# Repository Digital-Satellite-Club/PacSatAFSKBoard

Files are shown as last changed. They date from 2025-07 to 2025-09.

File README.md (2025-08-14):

# PacSatAFSKBoard
Hardware design for the PacSat AX5043 based board

This repository contains a board design for use in satellites for
packet message storing and forwarding and for general control.

It has a TMS570LS0914PGE processor for control and packet handling.
It uses 5 AX5043 chips for the radio interfaces, four receive channels
(uplinks) and one transmit channel (downlink).  Operation is full
duplex with receive on 144-148MHz and transmit on 430-440MHz.

Though it is designed for packet satellite, the design can be used for
any sort of full duplex dual band AFSK radio operation with or without
FM.  The AX5043 supports a large number of AFSK protocols (if you can
figure out how to program the AX5043).

With some filter redesign it could support a number of different
bands, too, maybe even up to 1280MHz.

The board also has MRAM storage for persistent data storage and an
RTC for timekeeping.  There's space on the board to add more things.

The board has a CAN interface and a serial interface on top of the
radio interfaces for interfacing to other boards in the system.

Output power is about 2 watts.  It has the ability to measure forward
and reflected power on the output.  It also has a sort of loopback
connector on the RF to test the receive and transmit chain.

The board is designed to be able to be used in an active/standby
configuration where you have two of the same boards and switch the RF
between the boards depending on which is active.

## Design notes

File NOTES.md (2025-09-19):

Notes on the AFSK Board
=======================

This keeps track of history, general information, things that need to
be done, and things that have been done.

The general information will probably make it into another document at
some point.

# TODO

Modify the board1/board2 resistor notes to say that putting in a 40K
resistor there (basically setting the voltage to 1V) will set the
board to be simplex.

The hardware watchdog needs to be able to be physically disabled so
the board can be programmed without the watchdog getting in the way.
Probably add a jumper by the JTAG and serial lines to disable the
watchdog.

On the CSKB standard, do we need to be able to operate as board 0?
That affects board layout.

According to the cubesat documents I have been reading, its best if
parts are automotive certified, AEC-Q100 or AEC-Q200.  I assume this
is so they can handle the shaking of the flight to space.  The
passives can all be certified for this, I'm pretty sure.  The only
connector you have to worry about is the PC104.  The chips and modules
are a different story.

Parts that are not automotive rated listed below.

|Part						|Function			  | Info |
|----						|---			  |----- |
| LMK1C1106A				| clock distributor | Suitable devices with 6 output not available.  Could use 4 output device (LMK00804B-Q1). Could use op amps (see https://www.analog.com/en/resources/analog-dialogue/articles/high-speed-amplifiers-make-clock-buffers.html). |
| O 16,0-JT22CT-A-P-3,3-LF	| oscillator | There don't appear to be any that are automotive and temp certified with 2.5ppm stability.  This one is temp, which is probably more important. There is one from TXC at 16.389MHz. |
| AS1016204-0108X0PWAY		| MRAM | No suitable devices available. |
| MAX31331					| RTC | No suitable devices available. |
| MP5073GG-P				| 1.2V current limiter | No suitable devices appear to be available. There is an MP5072 part that is AEC rated, basically the same chip but it's 1A instead of 2A. |
| MAX4995A					| 3.3V and 5V current limiter | Some devices are available from TI, like TPS2561-Q1 (dual channel) or TPS2557-Q1 (single channel). The MAX part may already be flight proven, though. |
| AX5043					| radio | No other option. |
| TQP7M9106					| PA | ? |
| QPL9547					| LNA | ? |
| AD4PS-1+					| RF power splitter | Environmental Specs seem good, probably ok. |
| QPC1022TR7				| RF switch | ? |
| ?							| PC104 connector | Unknown if AEC |

Part that are automotive listed below.

|Part						|Function			  | Info |
|----						|---			  |----- |
| STWD100NYWY3F				| Hardware watchdog |
| TCAN1044ADDFRQ1			| CAN bus interface |
| TMS570LS0914PGE			| CPU |
| TPS62A02AQDRLRQ1			| 1.2V power converter |
| TPS7A52-Q1				| 3.3V power converter |

I'm assuming that most ICs won't be a problem from the vibration point
of view.  The power modules are probably good to get certified, though.

Probably switch the analog switches dealing with active standby with a
set of zero ohm resistors.  That's a lot of resistors to switch,
though.  Populating 8 of 16 total resistors, maybe more with the UART
lines.  But there are advantages to a completely passive solution.

You could use one of the receive AX5043s ANTP1 port as an alternate
transmitter.  You could use the same PA or a different PA, either way
a QPC1022 RF switch could handle the choice.  You could even have
separate antennas.

Figure out temperature ratings on all parts and get as many to be 105C
or better as possible.  The outliers at the moment are:

    * RTC.  Probably only the MCP7940NT-E/MS from Microchip is
	  suitable, but it draws 20 times the standby power.
    * AX5043 - Not another option available.
	* AD4PS-1+ - Not sure about this one, perhaps three transformers
	  could be used.
	* TQP7M9106 - RF PA.  Could use a discrete device, but the parms
	  are pretty good.

The RX input filter can probably do the impedance adjustment for the
LNA, but I'm not sure how to calculate that.  There's an impedance
matching circuit in there now, removing it would save two parts.

Is there a reason the ANTP1 output of the AX5043 is connected to a 50
ohm resistor?  I can't find anything in the datasheet or errata about
that, it always shows it disconnected when not used. - May or may not
be necessary.

What UFL connectors can be removed?

Determine current limiter values, probably need to build a board and
measure.

# Done

Figure out how to hold the processor in reset until the power is good.
Need power good output from the converters, maybe switch to a
TPSM828302 for 1.2V and a LP3962 for 3.3V.

Replace big capacitors with smaller ones, if possible.

Move the TX chain to the right side of the board under the power
handling.

Move JTAG next to processor.

Replace the 4 512Kx8 MRAM chips with one 2Mx8 like the Avalanche 
AS1016204-0108X0PWAY.

Replace the DC/DC converters to ones that have the inductor built in,
to save space.

Move most power handling and watchdogs to the to right hand part of
the board.

Move the RX ax5043s to below and slightly left of the processor.  Move
the RF chain to below that.

Possibly rework board stack to have .1mm between the top layer and the
ground layer to reduce trace size required for 50 ohms.
(This was already done.)

Wire VER\_BIT2 to the PC104 connector.

Figure out the best way to handle the RX side of the AX5043 chips.  A
single-ended design would save a lot of board space because you can
get rid of one RF power splitter and the balun.  The AX5043 docs are
kind of sparse about how to do that, there's no mention of input
impedance on the receive side, and the transmit impedance info is
unhelpful.  But the full RF filter input as shown in the documentation
probably isn't required.  Maybe a balun on each RF input would be
enough to match impedance, since the signal is already filtered.

Replace receive side with LNA not requiring negative bias.  Probably
use a Qorvo QPL9547 due to its low NF.  Or maybe a GuerillaRF GRF2106W
which doesn't perform quite as well but uses a lot less power.

Put filters on each side of the LNA.

Make the 5V regulator optional or remove it.
(Removed, but space left for it.)

Possibly switch the MRAM and AX5043 SPI busses to simplify routine.

Figure out a way to disable the LNA from the CPU.

Find out why CURRENT\_FAULT\_U89 goes into two pins on the CPU.

Choose one oscillator and remove the other one.  Actually, just
replace with a "O 16,0-JT22CT-A-P-3,3-LF" from Jauch.

Neaten up the spacing on the AX5043s.

Add a thermsistor for the CPU.

Add CAN bus.

Add resistors to the MRAM SPI connection.

Does the JTAG interface need resistors on TCK and TDO (22 ohm)?
That's pretty standard.

The RF lines need some rework, some from the hybrid to the AX5043s are
kind of long, and they probably need to be coplaner.  I have added a
coplaner net class for this board stack (.225mm trace, .7mm spacing).

Shield on receive AX5043s.

Shield on transmit AX5043.

Decoupling, at least on 1.2V, seem inadequate.  Check that out.

Figure out how to orient the shields properly.

Add an option for a bleedoff inductor on the transmit output.

Via impedance

The chosen shield size for the AX5043s isn't tall enough.  The
transform is inside the shield, and it's 3.05mm tall, but all the
shields of the chosen size are 2.54mm tall.  I can't find a suitable
shield smaller than that to put the transformer on the outside.  The
shields with the proper height are way too big.  I can find a few that
are 12.7x13.2mm that are 3.5mm tall, but they would need to be
customized to add holes for traces.  You could just add a hole for the
transformer, I suppose.  Or get a custom shield.  Some of the shields
are pretty open on the top, like the PIC-S-201F, and the transformer
looks like it will go through the hole in top.  The transformer is
4.19x4.45x3.05mm, but that's the base dimensions, the transformer part
that comes up is smaller.  The opening int the top of the shield is
2.35mm at the narrowest point.  Estimating the size of the transformer
from the pictures, I get 2.2mm.  The opening starts 1mm from the
bottom of the shield, and that means the transformer would have to be
pretty close to the bottom.  However, after more analysis, I had the
orientation wrong, it's rotated 90 degrees from what I thought.  So
it's not going to work.

The RX shields are now the PIC-S-201F, the TX shield is the PIC-S-101,
but the RX shields will need some change.

In the shield problem, will the transformer coming up through a steel
enclosure affect the performance of the transformer?

Shield on RX input section.

Shield on TX PA section.

Check the inductor on the LNA, really verify the whole thing.

Change the 1.2V power controller to a MP5073.

The "Current Fault\_1V2" and "Current Fault\_3V3" are not connected to
anything and can probably be removed with their pull up resistor.  I
don't think there's much value in hooking it to the processor, if
either of these fire the processor will crash.

Do we need the capacitor between the LNA and the filter?  The filter
datasheet shows an input capacitor first, so that should block the DC.
The only concern would be the DC bias characteristic changing the
value of the capacitor.  I've asked MiniCircuits about this.
* This had to be added for other reasons due to the impedance matching
  circuit.

Write a document describing all the interfaces from the processor to
the rest of the board.

There may need to be a delay on the reset line from the power good
outputs because the power limiting circuits may take time to turn on.

The inductors for impedance matching the output of the LNA are on the
bottom of the board.  This isn't ideal, as they aren't in a shield,
but it's pretty crowded in the LNA shield.

I'm not terribly happy with the way the signal goes through the RX
input, but I'm not sure what to do about it.  I've improved it a lot,
but there's still a sharp turn on the inductor that leave the LNA are.
You might be able to rotate the LNA so the signal comes back towards
the center of the shield and then curves back around to leave, but I'm
not sure that's better.

The shields I have are steel, which is probably going to mess with the
inductors.  Need aluminum shields.

Clean up all the schematic notes and number all the device references
in a logical manner.

Add measurement of output and return power on TX.  I assume this can
be built with directional couplers, op amps, and the ADC on the
TMS570.

Analyze the RX input filter.

Figure out the AX5043 SPI routing.  Simulate the clock line in spice
to avoid possibility of double clocking, add proper resistors.

Add a thermsistor for the PA.

Route signals directly, don't use RF jumpers.

Rework transmit RF side.  At least replace the filter with a new one,
probably the LFCG-490+ from MiniCircuits, which also happens to be
temperature rated.

Look at replacing the second from bottom layer with a ground layer so
the bottom layer can be used to route RF traces.  This may not be
necessary, though, with careful layout. -- This was done for the RF
portions of the board, but not the digital or power areas.

On the output of the AX5043 transmit/input of the PA, there is each a
filter.  The one on the AX5043 has parts marked "NS", which I assume
means "don't populate".  The inductor is zero there.  C704 is also
marked NS on the PA sheet, which is most likely wrong.  Need to figure
all this out. -- Jim McCullers wrong a document on this, I just stole
his stuff.

Switch all the MAX4995 parts to the active high enable.  This will
make them all the same, avoiding confusion, and also make handling the
enable line easier since they will be pulled down.  It's hard to know
what to pull them up with.  It may not be good to drive the GPIO lines
with a pullup when the processor is powered off.  That will require
moving the enable flags to new GPIOs, but that's not a big deal.
Switch them to N2HET1[14] and N2HET1[20].

The TX AX5043 is powered off if "Alarm XMIT Shutdown" is activated by
the watchdog.  Do we really what this?  I think it would be good
enough to just power off the PA.  Will that work?  Powering down the
5043 means it has to be reprogrammed and it could really confuse
things if the part was powered down while something was talking to it
on the SPI bus.  I don't think it will hurt the PA to be driven while
powered off.

In fact, is the radio transmit killer really required?  If
FEED\_WATCHDOG is not toggled, the board will be powered off, and that
will accomplish the same thing.  It seems redundant.

The power shutdown IC on the TX AX5043 is different than the RX ones.
They should probably be consistent.

There is a +5V pullup through 10K on the LNA enable, and that line is
also driven by a TMS570 GPIO.  The pull up has to be there to disable
power when the board has power forced off.  I don't think it will be
an issue, but I'm not 100% sure there won't be an issue there when the
processor is driving 3V on the line.  If it is an issue, this could be
fixed easily with a FET.

Maybe add ferrite beads to the AX5043s' power inputs?

Why are there 4.7K resistors on the power inputs to the RTC?  And is a
diode needed on the VCC connection?  The diode on VBAT I can
understand, I think.  Also, VBAT voltage will be above VCC.  That
seems to be ok according to the data sheet, I think.  Also, maybe it
would be better to stick a big capacitor on VBAT.  A 220uF capacitor
would last around 94 hours at 5V, or 61 hours at 3.3v, by my
calculations.  That's the MAX31331, which uses 65nA on battery, and
there will be leakage in the capacitor (and diode if not trickle
charging) that will probably shorten the time. - Rework this to
increase the size of the Vbat capacitor and not use the VCC one, just
do a normal decoupling cap there.

Move the RTC away from the power conversion section to avoid it
getting too hot.

What does the HW\_SENSE (Pin 6 on CPU) do? - Get rid of it

Does it make sense to wire the UARTs to the PC104?  If so, do we need
two of them on the PC104?  Shouldn't one go to a separate connector
somewhere?  If so, which one?  UART1 is a standard UART, UART2
supports "Local Interconnect standard 2.0" which is probably better
for an interconnect.  So UART1 (SCI) should go to the local connector
and UART2 (LIN) should go to the PC104, I think.  More info: the LIN
bus requires special hardware, it's not just a serial connection.
Yes, put a connector on there so the UART1 pins are available, maybe
run to the PC104, too.

The LNA doesn't have a current limiter on it.  It's best to power it
with +5V (it will work on +3.3V, but it doesn't perform as well).  You
don't want to put it on the PA power lines, as you may want to power
off the PA while still receiving.  Maybe another current limiter is in
order?  Yes

Add 3 more MRAM parts.

Do we need all those wire holes?  A few I can understand, for powering
the board on the bench, but there are a bunch of them, some with just
grounds.  Need to figure out their purpose. - Used for scope clips.
Need to add a few more.

The 3.8K resistor on HW\_POWER\_OFF\_N is a strange value.  Can it be
a more normal 4.7K or 10K?  Yes

Add more vias around the ground areas in RF.

Probably add another CAN bus.

Figure out what happens when the two lockstep processors lose sync.
If one of the processors goes bad, is there a way to just run with one
processor?  - If there is a lockstep error, a software interrupt is
generated and software must handle it.  The processors cannot run
independently, they can only run in lockstep or in certain test modes.

Maybe switch to 0402 parts along the RF path to reduce stray
inductance and capacitance and reduce size.  And perhaps don't use
handsolder, as the pads are larger and thus have more
capacitance/inductance.  Maybe 0402 parts on the rest of the board to
get more space.

Add enables to the CAN bus transceivers?  The chip does not really
have an "off" state, it's a "standby" state where it's listening on
the bus but cannot transmit.

Fix DC bias issue on the output impedance filter of the LNA.

Replace PA output filter.

The RBP-140+ 140MHz filter is kind of expensive, though fairly
compact.  It's also not temperature rated.  Maybe it could be replaced
with discrete components?

The HW\_POWER\_OFF\_N line needs to disable the 3.3V current limiter
since there is no longer a 3.3V regulator.

Implement the "Attached" line from the PC104 to inhibit the
transmitter, if necessary.

Do steel RF shields affect the inductors under or around them?  Is
aluminum better?  - No one was sure, maybe it's non-magnetic steel?
We will just have to try it out.

Is the output filter on TX enough?  It's >50db at 800MHz and 1.6GHz.
You get some filtering from the impedance matching network, too.
 - Need to measure and see.

There's a note in the schematic about biasing the 5043 inputs, but I
can't find any info on that.  It's on the RF Input sheet.  Need to
figure out if that's something that needs to be done.  I don't really
understand the comment, though. - The comment was from an app note
that Bob read that the inputs on the 5043 apparently work better if
biased to about 1V.  He can't find the app note any more.

The PC104 connector is actually two connectors, a 64-pin (4x16) one
and a 40 pin one (4x10) per the PC104 web side.  I've actually more
seen two 2x52 connectors more often on schematics.  Need to figure out
how to represent that. - Pulled the design from the Pumpkin Space
documents.

The 78nH inductors in the AX5043 input section don't come in very high
Q values, 28 is the best you can get (and only from Murata).  77 and
79nH are even worse. - Actually, 38@143MHz is what the inductor is, so
that's not too bad.  Not much different than the Coilcraft ones.

The MRAM parts are WSON packages.  SIOC packages are available, too.
SIOC is somewhat bigger, but might be better from a thermal point of
view.

Figure out what to do with the UART pins on the PC104 when dealing
with active/standby.  Really just figure out what to do with the UART
pins. - UART pins are not currently used.

Figure out where the external RF connections need to be so the layout
can be simplified around that. - We are putting the RF connections on
UF.L connectors to simplify things.  We will glue on a cable for
testing and for flight.

Probably remove the L1/L2 inductor on the AX5043s and replace them
with a short.  I don't think we will use them. - Needed for 2M to
work, need to get the inductor value.

After the MRAMs and second CAN bus, GPIOs are running short.  We have
some options.  A 2-4 decoder could do this, but you would also need an
enable (and thus pullups), and it would really only recover one GPIO.
Another option is an I2C or SPI to GPIO device.  The AX5043s each have
5 pins that can be used for GPIOs, though that means if an AX5043
fails you can't use those GPIOs.  The interrupts from the AX5043s
could be or-ed together, but you would have to scan all of them if you
got an interrupt. - Removed a lot of the connections to the bus as
they aren't needed.

# Not going to do

Rotate the CPU so that fewer traces need to be routed under the CPU.
Perhaps replace the CPU with a BGA version to save space, the BGA is
16x16mm verses 22x22mm for the flat pack.  This could also provide
more FLASH and RAM space. -- Moving a few lines around the processor
made a huge difference.  This is not necessary.

Maybe put the directional coupler on the layer under the transmit
trace instead of beside it?  The coupling would be better but I would
need to calculate the coupling.  But this is just a maybe, what's
there is probably good enough.  Don't want to steal too much power
from the transmitter.

There are now individual power enables on each AX5043.  Do we need the
main one?  The problem is we would need a lot of processor GPIOs that
are pulled down by default, or we would need to switch to power chips
with active low enables.  Plus there is then no power limiting.
Probably not a good idea.

Why is both the RTC and the hardware watchdog controlling the transmit
shutdown?  It would seem only one or the other would be necessary.
The whole transmit shutdown thing has been removes, so this is no
longer relevant.

# RF Shields

RF shields cover all the RF sections possible to cover.  There are 7
shields and they use standard shield sizes.  The bottoms are
castellated and surface mount.

Six shields cover the AX5043s and the RF input section are 12.7mm
x 13.67mm (.5"x.538") and the one that covers the PA is 26.21mm x
26.21mm (1.032"x1.032").  There are options from at least TE
Connectivity AMP Connectors, Leader Tech Inc, Laird Technologies EMI,
and 3G Shielding Specialties LP.

The traces running in and out of the shields are done in a way to
accommodate all these shields, though not all have been checked.

I assume shields should be non-magnetic to avoid issues with inductor
coupling.  It's hard to find two-piece shields where the frame is
aluminum, though.  I'm not sure of the requirements around this,
though.

# History

## 2025-07-23

The pins for AX5043\_PWR\_CTL moved (and I think was renamed) and there
is a new PA\_PWR\_CTL line.

The Address notes on the two MAX31725MTA+ temperature sensors were
backwards.  Switched the notes so they match the schematic.

VER\_BIT2 is not wired to the PC104.

## 2025-07-24

Fixed all wiring that was wrong due to schematic changes.

Changed the RTC crystal to a SMD one and remove the capacitor.  The
datasheet says no capacitor is required.

Cleaned up some crazy traces.

## 2025-07-25

Reworked the board, basic layout is done and most details are handled.
Left to do:

* Clock handling

* Rework of the TX power amplier.

* Hooking everything up.

* The rest of the TODO list.

There should be no software visible changes from the changes today.

Remove the DS28E83Q+T crypto processor.  Nobody knew why it was there,
there was no software for it, and it wasn't practical.  Since there is
no onewire hardware on the CPU, it would have to be bit-banged, and
that would cost 50 times the CPU of just doing the crypto on the
CPU.

## 2025-07-26

Change the DC regulators to ones with power good pins and tie that in
to processor reset.

Removed the HW\_POWER\_OFF\_N signal to the CPU.  The CPU is going to be
instantly powered off if that is not asserted; there's not much value
in sending it to a GPIO.

Remove the UART\_RTS and UART\_CTS connections.  The chip doesn't
support these lines, no point in having them.

Switched the MRAM and AX5043 SPI busses to simplify routing.  MRAM is
now on MIPSPI3, the AX5043 is on MIBSPI1.  This puts the AX5043 SPI
connection on the bottom of the processor by the AX5043s, and the MRAM
SPI where there is plenty of room to add MRAM devices as necessary.

Move AX5043\_SEL1 from pin 24 to pin 90
Move AX5043\_SEL2 from pin 33 to pin 91
Move AX5043\_SEL3 from pin 35 to pin 92
Move AX5043\_SEL4 from pin 35 to pin 96
Move AX5043\_SEL\_TX from pin 124 to pin 97

Added an LNA\_ENABLE control on pin 89.

Removed the CURRENT\_FAULT\_U89 signal from pins 73 and 74.  They don't
go anywhere else and serve no purpose I can tell.

Clocks are all set up and wired in.

MRAM is wired in.

## 2025-07-27

Wired in the AX5043 SPI busses and all their control lines.

Added the following connections to the CPU:

AX5043\_EN\_RX1 to pin 36
AX5043\_EN\_RX2 to pin 35
AX5043\_EN\_RX3 to pin 33
AX5043\_EN\_RX4 to pin 32

Added a thermsistor to AD1IN\_16.

The I2C temperature sensors are removed.

A thermsistor by the CPU was added to pin 58.

## 2025-07-28

Added calculations for the Qorvo TQP7M9106 to get Zin and Zout for the
frequency in question.

Rework the output PA to use a Qorvo TQP7M9106.  The old part was not
recommended for new designs, and the Qorvo part seems more efficient.
Do all the matching and such for that.

Added a termsistor by the PA.

Did simulations of the RF input and adjusted accordingly.

Did simulations of the AX5043 TX output.

Add a CAN bus.

Added a resistor to the MRAM SPI clock signal.

Add SMA connectors for TX and RX.

Added resistors to JTAG interface, per the way it's defined.

## 2025-07-29

Replaced UFL connectors with surface mount ones.

Added shields for the TX and RX AX5043 sections.  They are
12.7mmx13.67mm (.5"x.538").  That seems to be a pretty standard size,
lots are available.

Added a bunch of decoupling caps on the CPU, basically one per CPU,
like the launchpad did, and like is standard.

Switched the RX AX5043 shields to PIC-S-201F.  It appears that if
oriented correctly the transformer will stick through the hole without
a radial line on it.  The TX one was left as PIC-S-101, as it doesn't
have a transformer in the can and doesn't need the extra height.  Both
parts have the same base layout.

Sized up some power lines for safety margin.

Calculation of the via impedance (done at Sierra Circuits proto
express) comes out to ~52 ohms.  The board is 1.56mm thick (JLCPCB
2116 board stack), each copper layer is .035mm.  Input is:

  Height of dielectric - H1 ( mm ) - 1.416
  Dielectric Constant Er\_1 - 4.5
  Height of dielectric - H2 ( mm ) - .109
  Dielectric Constant Er\_2 - 4.5
  Dielectric Constant Er\_3 - 1
  Via Diameter ( mm ) - .308
  Anti Pad Diameter ( mm ) - 1.53
  Annular Pad Diameter ( mm ) - .508
  Via Pad Diameter ( mm ) - .508
  Via Plating Thickness ( mm ) - .035
  Annular Pad Thickness ( mm ) - .035
  Reference Plane Thickness ( mm ) - .035

Reroute the SPI clock to the bottom of the board where it can be
impedance controlled to 50 ohms.  Add a ground plane on the bottom to
the entire RF section so that the impedance is the same as on the top.

Simulated the AX5043 SPI clock and set the resistor values to 470 ohms
and added a resistor for the end device, too.  With the current
settings, assuming a .2ns rise time from the processor, this gives a
fairly smooth signal on all the inputs.  The signal reaches 2.8V (from
0 to 3V input) or .2V (from 3V to 0) in 2ns.  Resistance values 330
and down give some issues at the RX2 input, there is a dip that could
be double-clocked on.  Higher values will slow the rise time more.
With this setup, no resistors on the other lines, as long as they
settle within half a clock period plus 2ns, all should be good.  You
could probably run this at 100MHz without an issue.  But the double
clocking is the big problem.

## 2025-07-30

To solve the problem with the transformer not fitting in the shield,
replace the transformer with a lumped sum balun as described by the
work Jim McCullers did in the "AX5043 Receiver Impedence Matching"
document.  I just used the values he came up with.  Changed all the
shields back to the PIC-S-101.  Also changed the zero-ohm resistor
from the RF splitter to the AX5043 to a decoupling capacitor.

Changed the zero-ohm resistor between the TX AX5043 and the PA to a
decoupling capacitor.

Changed the shields on the AX5043 to PIC-S-201F which is a frame and a
cover.  This can be replaced with a PIC-S-101 which is a single unit
when access is no longer needed to the parts underneath.

Added a shield for the TX PA and RX input sections.

Add a thermsistor for the power conversion area to pin 83.

Rework the RF input circuitry.  I had to increase the power feed
inductor and add an input and output impedance match circuit.  That
required changing the parts around the LNA to 0402 size to get them to
all fit.  You might be able to modify the input filter to adjust the
impedance, but I couldn't figure out how to do that to match a complex
impedance.  I'm sure it can be done, but it's a matter of how.

## 2025-07-31

Replaced the 1.2V current limiter/switch with a MP5073GG from
Monolithic Power.  The MAX4495 that was there wasn't rated for 1.2V.

Remove the Current Fault lines for 1.2V and 3.3V.  They didn't go
anywhere, and there's not much the processor could do about it if they
went bad.

Removed the zero ohm resistors on WDO\_N, the enable line feeding the
current limit switches enables.  There's already a way to turn of the
watchdog on the watchdog chip, so it doesn't seem necessary.  Plus the
line needs to be driven to work.  Also renamed WDO\_N to POWER\_ENABLE
to better reflect what it does.

Wired in the power good pin on the MP5073GG-P to the processor reset
so that the processor is held in reset until 50us after the chip
enabled power.

Cleaned up the hierarchical sheets and re-annotated everything to make
copying and pasting easier.

Reworked the LNA input and output impedance matching so nothing had to
be on the bottom of the board.  Switched the positions of the
capacitor and inductor in the L match, that let me match more closely
with single standard parts instead of having to use two inductors.

## 2025-08-01

Improved the LNA layout some more.  I have one part rotated at 45
degrees to round a corner a little better.  It's not required, but
it's supposed to be better for RF flow.

Rotate the RF filter after the LNA to improve flow and do some more
cleanups.

Reworked the LNA some more, I think I'm happy with the layout now.

Widened the bandwidth of the input filter.  That reduces the inductor
values to ones that are obtainable.

Switch to aluminum shields.  A number of shields are possible to use,
see notes.

Update the RF input filter again for wider bandwidth to get a 180nH
inductor, something low enough to fit into a 0805 part with a decent
Q.  Annotate the schematic with the Q values of the various inductors
that I was able to find.

Snug in the 3.3V LDO a bit more to give more space on the side.

## 2025-08-03

Add a directional coupler and power measurement chips (ADL5501AK) to
feed into the ADCs (Forward power to pin 74 AD1IN[3] and reverse to
pin 73 AS1IN[2]) and an enable for those parts into pin 124
N2HET1[12].  Pin 124 is pulled down by default, so the chips will be
disabled at reset.  The direction coupler is 4mm long with .1524mm
traces .127mm apart.  At full power out (+33dBm) this will result in
about -7dBm of power from the coupler.  This was simulated with a
transmission line in qucs.  The voltage for that can be calculated
from the chip manual.

Fixed an issue with the 3.3V power controller.  The 1.2V controller
part (MP5073GG-P) is an active high enable, the MAX4495ALAUT is an
active low enable.  So switch out the 3.3V controller with a
MAX4495AAUT (which has an active high enable), but leave the other two
with the AL version of the part.  The WDO_N output from the hardware
watchdog is active low, but the logic is backwards, when the watchdog
fires (goes low) we want it to disable the power.  I think this was
wired incorrectly in the REVC and REVD schematics.

Added a pull up on LNA\_ENABLE\_N so that the LNA is disabled even
when the rest of the power to the board is off.

Switch the logic on AX5043\_PWR\_CTL from active low to active high by
switching from the MAX4495ALAUT to the MAX4495AAUT.  Rename it to
AX5043\_PWR\_EN.  Move it from pin 98 to pin 141 so that it's pulled
down by default in the processor, too.  Still need the external pull
down in case the processor is turned off.  Pulling that line up was
problematic, as you don't really want to use +3.3V (will be off if
power is externally disabled) or REG_3V3 (driven if processor is
powered off).  Also this makes all the parts the same, making
inventory easier.

Do the same with PA\_PWR\_CTL -> PA\_PWR\_EN, move from pin 99 to pin
125.

Make the AX5043 TX power control chip the same as the ones on the RX
chips, just to be consistent and have one less chip to worry about.

Remove the PA power watchdog.  It's not doing anything useful.  It's
driven by the same watchdog line as the main watchdog, and if the main
watchdog fires it's going to power off everything, resulting in the PA
being powered off.  There were other issues, too, as it would power
off the AX5043 TX chip, too, which could cause bad things to happen if
the SPI bus was talking to it at that time.  But it didn't really
matter, the processor would be powered off, anyway.

Add a AX5043\_EN\_TX line to pin 100 of the CPU to control the power
to the AS5043 TX device.

Move the LNA\_ENABLE to pin 118 so it's a pull down by default and
rework the LNA enable so the +5V is not applied to a GPIO pin
directly.  Go through a MOSFET instead.

## 2025-08-04

Change the LNA\_ENABLE MOSFET to a BSS138, just to choose something
common.  Also fix the footprint.

Change the AX5043 power control chips to be MOSFETs.  No need for
something complicated.  Use P-Channel enhancement mode MOSFETs, so the
enable has to be pulled down to turn on the MOSFET.  Rename the
enables to add a \_N for negative logic.

Rename the AX5043 select lines to add a \_N because they are negative
logic.

Remove the connection from KELVIN\_GND to ground.  According to the
TMS570 data sheet, that pin should not be connected to any other
ground.  I don't think it matters, it's only for crystals, but it
should probably be left floating.

## 2025-08-05

Fixed some part values, used 4.1p style, not 4p1.

Add a pin 1 indicator to a couple of ICs that didn't have it.

Moved AX5043\_EN\_TX\_N from pin 100 to pin 89 and
AX5043\_EN\_RX\_4\_N from pin 32 to 24.  This frees up all the
necessary MIBSPI5 lines for possibly adding another SPI bus on
the board.

Fix the footprints on the diodes on the RTC.

Update the ferrite beads with actual values.

Add ferrite beads to the AX5043s' power inputs.

Changed the clock buffer from a CDCLVC1106 to a LMK1C1106A.  It
temperature rated, has better specs, and is cheaper, and drop in
compatible.  Looking at the power usage, it's hard to tell.  It looks
like the specs were misinterpreted for the CDCLVC1106, the power given
on the graph was per pin, so it would really be around 20ma, the same
as given for the LMK1C1106A.

## 2025-08-07

Increase the size of the Vbat capacitor on the RTC and do not use the
VCC one, just do a normal decoupling cap there.

Move the RTC to the other side of the board to keep it away from
things generating heat.

Remove the HW\_SENSE (Pin 6 on CPU) line.  It was used on a dual CPU
system to tell which CPU was which, not relevant here.

Add a local connector to UART1 to make it easier to plug in an
external connector.  Still left it on the PC104 along with UART2.

Add a power limiter for the LNA.

Add 3 more MRAM parts.

## 2025-08-08

Added a series termination on the CPU clock.

Modified the resistor on the LNA power limiter to be 200ma.

Move the JTAG connector to the edge of the board so it's accessible in
a board stack.  This required moving some things around, but no big
deal.

Add some wire holes around the LNA and PA.

Change the 3.8K resistor on HW\_POWER\_OFF\_N to a more normal 4.7K.

Sprinkle vias all over the coplanar areas.

Reworked MRAM devices to put pull-ups on the WP and IO3 pins instead
of direct ties to +3.3V.

Add a second CAN bus for redundancy.

## 2025-08-10

Fix some values on the PA and rearrange a bit to get the inductors
away from each other.

## 2025-08-12

Removed the version lines going to the PC104.  They get in the way and
I can't imagine what use they would have.  They can be re-added if
necessary.

Moved things around at the bottom of the board to make room for the
active/standby RF circuitry.

Added support for active/standby boards in the hardware.

## 2025-08-13

Change transmit power dissipation resistors to 2W.

Moved ACTIVE\_N to a normal GPIO so it can be interrupt driven.

Add OTHER\_HW\_POWER\_N to a GPIO so in the externally driven
active/standby case the other power state can be monitored.

Added a test mode using the RF switches to shunt power from the
transmitter to the receiver for an RF loopback test.

## 2025-08-14

Changed SMA connectors to vertical ones.

Change SMA TX/RX connectors to U.FL connectors.  For development I
will epoxy down a U.FL to SMA cable to the board.  For deployment
various options exist, including UFL or soldering cables directly to
the board and epoxying them down.

Get rid of the GPADC zero-ohm resistors on the receiver AX5043s.
Those cannot be used when receiving, and their use is questionable,
anyway.  Leave it on the transmitter one as that could still be used.

## 2025-08-15

Change many of the passives to 0402s to make more room and reduce
parasitics.

Add a current limiter for the onboard +5V devices, create a new power
rail named +5VAL for all the devices that need to be powered up even
when the power is off.

Add enable controls for the CAN bus transceivers.

Fixed the RF input and output filters.  Added a simulation for the
RF output filter.

Fixed DC bias issue on the output impedance filter of the LNA.

## 2025-08-16

Rework the output filter.  The part that was chosen really wasn't
suitable, it didn't have good thermal or vibration characteristics and
it wasn't enough filtering.  Switch to a discrete filter.

Change 3.3V power convert to a TPS7A52-Q1.  It's AEC rated.

## 2025-08-18

I spent practically a whole weekend trying to figure out how to
measure impedance matching circuits.  This probably has more general
applicability to power measurement in general, but in spice measuring
power on a signal that is complex is problematic.  I think the problem
is that you don't have a complex representation of the current, you
get bizarre values out of it if you do a simple V * I.  And doing
V^2/R is hard if R is complex and you don't really know the value.  I
don't think these thing make any sense, in general, and I don't know
how to directly measure the power in a complex signal.

However, I have figured out a way around it.  When you have an L
match, you have a component facing the complex impedance.  You can put
another component in front of the filter to remove the complex
impedance from the signal (just basically match the input imaginary
impedance with the corresponding value).  Then adjust the component
of the L match facing the complex impedance.

Examples are in order.  Start with an easy case.  Suppose we have an
output impedance of 6.23 - j13.3 at 435MHz.  If we plug that into a
smith chart or an impedance matching program, we get two possible
outcomes.  The first is a 10.9nH series inductor and a 19.4pF parallel
capacitor.  Just split the inductor into two, 4.87nH (j13.3 ohms at
435MHz) then 6.03.  Then the capacitor.  Take your power measurement
between the two inductors.

The other possibility is a 113.9pF series capacitor followed by a
6.9nH parallel inductor.  You can't just split the capacitor into two.
Or, from a smith chart representation, the first value does not pass
over the zero imaginary impedance line.  But we can use the same
4.87nH inductor before the capacitor to bring the value to zero
imaginary impedance, then adjust the capacitor value (to 22.1pF) and
measure between the inductor and capacitor.

If you have a parallel device facing the complex impedance, you can
split it in to in parallel (if that work) or as in our second example
put a device between to cancel the complex impedance.

From the simulation you can also put the resistor first after the
voltage source and measure before it goes into the capacitor or
inductor.  The simulations were modified to do this.

## 2025-08-20

Remove the UART connections from the PC104.  It's unknown if they are
needed, and if they are then they will need work for active/standby.

## 2025-08-23

Lots of work on the various parts to make the board more
manufacturable.  Changed some values from hard to get values and
changes the strings in the values to be used more easily.

Moved the RF splitter over a bit to make room for another .5" square
shield in case we switch to discrete components for a filter.

## 2025-08-25

Replace the RBP-140+ on the LNA output with discrete components.  They
should perform better and be certified.

Change the inductors on the RF input filter to a larger part with a
lower series resistance to decrease the loss in the filter.

## 2025-08-26

After spending some time looking at how real inductors work, I've come
to the conclusion that the RBP-140+ wasn't so bad.  When assuming a Q
of 35 at 150MHz and using that resistance, it comes out that the
elliptic filter I was using had 8dB of loss and the RF input filter
had 2.5dB of loss.  In fact, the stats of the RF input filter were
very similar to the RBP-140+, except that has very even group delay.
All this needs to be re-thought.

The filter simulations were all reworked based upon how Q actually
works.  Redid the RF input filter to a lowpass elliptic filter, which
lowered the loss and give room for bigger inductors with higher Q.
All the inductors are reworked.

Added a resistor to the bleed off inductors to avoid it affecting the
performance of the filter.  Since it's on the other side of the
inductor I don't think it will add noise (maybe?  Not 100% sure.)

Looked at capacitance of the inductors.  The only significant change
was in the RF input filter, since it had a parallel capacitor of 1.2pF
and a capacitance of .18pF.  Added inductor capacitors to the
simulations, but they didn't make much difference elsewhere.

## 2025-08-27

Switched over to the CubeSat Kit Bus board configuration.  Replaced
the PC104 connector with the actual correct part, the one that was
there was not suitable.  Lots still left to do here.

## 2025-08-28

Modified the BOM file fixer to output an XLS file instead of a CSV
file.  The omega symbol (for ohms) is properly handled from XLS files,
it is not from CSV files.

Removed all the unknown PC104 signals.  The LTM doesn't have them, it
has other things, will need clarification.

Rework board layout some more, finish up temporary PC104 assignments.

## 2025-08-29

Add an AND gate to the logic for POWER\_ENABLE so that it is
controlled by both the watchdog and the HW\_POWER\_OFF\_N line.

## 2025-09-01

Rework board to be the Fox Plus setup.  Saved the old configuration in
the CSKB_Base tag.

Convert MRAM parts into SIOC packages for more reliability with
thermal cycling.

## 2025-09-01

Rework the TX side to fit into two small shields.  This required
removing the unused TX filter after the AX5043.  I believe it has been
proven to not be needed.

Replace the 1.2V regulator with a non-module one (automative rated)

## 2025-09-04

Added an option to allow 1.2V to come from 3.3V or 5V.

## 2025-09-07

Add connections to CSKB I2C pins, which look pretty standard.

## 2025-09-08

Switched back to the CSKB board.

## 2025-09-09

Added a bypass resistor so the power off pin can still available if
the digital switches use for setting the board number are removed.

Add an optional way to derive 3.3V from 5V.

## 2025-09-16

Added a pull-up resistor to the clock distributor instead of tying
the enable directly to ground.

Removed a redundant pull up on the HW\_POWER\_OFF\_N line.

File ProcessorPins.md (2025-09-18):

IO Connections on the PacSat AFSK processor
===========================================

These are the pins on the TMS570 processor, where they go, what they
do and some notes at the end with some more details.

The "G" column shows the GPIO usage and capability.  The first letter
is how the GPIO is used: I for input, O for output, B for
bidirectional, blank if not used as a GPIO, and ? if the function is
not known (the PC104 pins).  The second letter is U for pullup by
default and D for pulldown by default or blank if the pin cannot be
used as a GPIO.

|Pin3	|CPU Pin Name			|Schematic Name			|G |Description |
|----	|---			|---			|--|--- |
|1		|GIOB[3]				|OTHER\_FAULT\_N		|ID|Fault line from other board |
|2		|GIOA[0]				|						| D|free gpio|
|3		|MIBSPI3NCS[3]			|I2C\_SCL				|OU|RTC control (MAX31331TETB+) |
|4		|MIBSPI3NCS[2]			|I2C\_SDA				|BU|RTC control (MAX31331TETB+) |
|5		|GIOA[1]				|AX5043\_IRQ\_RX1		|ID|Interrupt from AX5043 RX1 |
|6		|N2HET1[11]				|OTHER\_HW\_POWER\_OFF\_N|ID|Power off state for the other board |
|7		|FLTP1					|						|  | |
|8		|FLTP2					|						|  | |
|9		|GIOA[2]				|OTHER\_PRESENCE\_N		|ID|Presence line from other board |
|10		|VCCIO					|						|  | |
|11		|VSS					|						|  | |
|12		|CAN3RX					|CAN\_A\_RX				|IU|CAN bus transceiver |
|13		|CAN3TX					|CAN\_A\_TX				|OU|CAN bus transceiver |
|14		|GIOA[5]				|AX5043\_IRQ\_RX4		|ID|Interrupt from AX5043 RX4 |
|15		|N2HET1[22]				|						| D|free gpio|
|16		|GIOA[6]				|OTHER\_ACTIVE\_N		|ID|Active line from other board |
|17		|VCC					|						|  | |
|18		|OSCIN					|						|  | |
|19		|Kelvin\_GND			|						|  | |
|20		|OSCOUT					|						|  | |
|21		|VSS					|						|  | |
|22		|GIOA[7]				|AX5043\_IRQ\_RX3		|ID|Interrupt from AX5043 RX3 |
|23		|N2HET1[01]				|						|OD|Yellow LED |
|24		|N2HET1[03]				|AX5043\_EN\_RX4\_N		|OD|Power enable for AX5043 RX 4 |
|25		|N2HET1[00]				|						|OD|Red LED |
|26		|VCCIO					|						|  | |
|27		|VSS					|						|  | |
|28		|VSS					|						|  | |
|29		|VCC					|						|  | |
|30		|N2HET1[02]				|						|OD|Green LED |
|31		|N2HET1[05]				|LNA\_ENABLE			|OD|Used to enable the LNA |
|32		|MIBSPI5NCS[0]			|						| U|free gpio (Save for extra SPI if possible) |
|33		|N2HET1[07]				|AX5043\_EN\_RX3\_N		|OD|Power enable for AX5043 RX 3 |
|34		|TEST					|					 |  | |
|35		|N2HET1[09]				|AX5043\_EN\_RX2\_N		|OD|Power enable for AX5043 RX 2 |
|36		|N2HET1[04]				|AX5043\_EN\_RX1\_N		|OD|Power enable for AX5043 RX 1 |
||||||
|37		|MIBSPI3NCS[1]			|MRAM\_NCS3				|OU| |
|38		|N2HET1[06]				|UART\_RX1				|ID|PC104 pin 92 |
|39		|N2HET1[13]				|UART\_TX1				|OD|PC104 pin 88 |
|40		|MIBSPI1NCS[2]			|MRAM\_NCS2				|OU| |
|41		|N2HET1[15]				|CAN\_A\_EN\_N			|OD|CAN bus A transceiver enable |
|42		|VCCIO					|						|  | |
|43		|VSS					|						|  | |
|44		|VSS					|						|  | |
|45		|VCC					|						|  | |
|46		|nPORRST				|						|  | |
|47		|VSS					|						|  | |
|48		|VCC					|						|  | |
|49		|VCC					|						|  | |
|50		|VSS					|						|  | |
|51		|MIBSPI3SOMI			|MRAM\_MISO				|IU| |
|52		|MIBSPI3SIMO			|MRAM\_MOSI				|OU| |
|53		|MIBSPI3CLK				|MRAM\_CLK				|OU| |
|54		|MIBSPI3NENA			|MRAM\_NCS1				|OU| |
|55		|MIBSPI3NCS[0]			|MRAM\_NCS0				|OU| |
|56		|VSS					|						|  | |
|57		|VCC					|						|  | |
|58		|AD1IN[16] / AD2IN[0]	|\*						|  |Thermsistor near the processor |
|59		|AD1IN[17] / AD2IN[01]	|						|  |free adc |
|60		|AD1IN[0]				|						|  |free adc |
|61		|AD1IN[07]				|PWR\_FLAG\_AX5043		|  |Power flag from the AX5043 current limiter |
|62		|AD1IN[18] / AD2IN[02]	|						|  |free adc |
|63		|AD1IN[19] / AD2IN[03]	|						|  |free adc |
|64		|AD1IN[20] / AD2IN[04]	|VER\_BIT0				|  |Board version number bit 0 |
|65		|AD1IN[21] / AD2IN[05]	|VER\_BIT1				|  |Board version number bit 1 |
|66		|ADREFHI				|						|  | |
|67		|ADREFLO				|						|  | |
|68		|VSSAD					|						|  | |
|69		|VCCAD					|						|  | |
|70		|AD1IN[09] / AD2IN[09]	|						|  |free adc |
|71		|AD1IN[01]				|						|  |free adc |
|72		|AD1IN[10] / AD2IN[10]	|PWR\_FLAG\_5VAL		|  |Power flag from the +5VAL current limiter |
||||||
|73		|AD1IN[02]				|REV\_PWR				|  |\*Reverse RF TX Power |
|74		|AD1IN[03]				|FWD\_PWR				|  |\*Forward RF TX Power |
|75		|AD1IN[11] / AD2IN[11]	|PWR\_FLAG\_LNA			|  |Power flag from the LNA current limiter |
|76		|AD1IN[04]				|PWR\_FLAG\_SSPA		|  |Power flag from the PA current limiter |
|77		|AD1IN[12] / AD2IN[12]	|						|  |+5V power measure, linear from 0-2.5V |
|78		|AD1IN[05]				|						|  |free adc |
|79		|AD1IN[13] / AD2IN[13]	|						|  |+1.2V power measure, 0-1.2V |
|80		|AD1IN[06]				|						|  |+3.3V power measure, 0-1.65V |
|81		|AD1IN[22] / AD2IN[06]	|						|  |free adc |
|82		|AD1IN[14] / AD2IN[14]	|						|  | Board version number bit 2 |
|83		|AD1IN[08] / AD2IN[08]	|\*POWER\_TEMP			|  |Thermsistor in power conversion section |
|84		|AD1IN[23] / AD2IN[07]	|\*PA\_TEMP				|  |Thermsistor near the PA |
|85		|AD1IN[15] / AD2IN[15]	|						|  |Board version number bit 3 |
|86		|AD1EVT					|						| D|free gpio |
|87		|VCC					|						|  | |
|88		|VSS					|						|  | |
|89		|CAN1TX					|AX5043\_EN\_TX\_N		|OU|Power enable for AX5043 TX |
|90		|CAN1RX					|AX5043\_SEL1\_N		|OU|SPI chip select for AX5043 RX1 |
|91		|N2HET1[24]				|AX5043\_SEL2\_N		|OD|SPI chip select for AX5043 RX2 |
|92		|N2HET1[26]				|AX5043\_SEL3\_N		|OD|SPI chip select for AX5043 RX3 |
|93		|MIBSPI1SIMO			|AX5043\_MOSI			|IU|SPI MOSI for all AX5043s |
|94		|MIBSPI1SOMI			|AX5043\_SIMO			|OU|SPI SIMO for all AX5043s |
|95		|MIBSPI1CLK				|AX5043\_CLK			|OU|SPI clock for all AX5043s |
|96		|MIBSPI1NENA			|AX5043\_SEL4\_N		|OU|SPI chip select for AX5043 RX4 |
|97		|MIBSPI5NENA			|AX5043\_SEL\_TX\_N		|OU|SPI chip select for AX5043 TX |
|98		|MIBSPI5SOMI[0]			|						| U|free gpio (Save for extra SPI if possible) |
|99		|MIBSPI5SIMO[0]			|						| U|free gpio (Save for extra SPI if possible) |
|100	|MIBSPI5CLK				|						| U|free gpio (Save for extra SPI if possible) |
|101	|VCC					|						|  | |
|102	|VSS					|						|  | |
|103	|VSS					|						|  | |
|104	|VCCIO					|						|  | |
|105	|MIBSPI1NCS[0]			|CAN\_B\_EN\_N			|OU|CAN bus B transceiver enable |
|106	|N2HET1[08]				|						| D|free gpio|
|107	|N2HET1[28]				|						| D|free gpio|
|108	|TMS					|JTAG pin				|  | |
||||||
|109	|TRST					|JTAG pin				|  | |
|110	|TDI					|JTAG pin				|  | |
|111	|TDO					|JTAG pin				|  | |
|112	|TCK					|JTAG pin				|  | |
|113	|TCK					|JTAG pin				|  | |
|114	|VCC					|						|  | |
|115	|VSS					|						|  | |
|116	|nRST					|\*Processor\_Reset		|  |Main reset pin for the processor |
|117	|nERROR					|FAULT\_N				|  |Output ERROR line from the processor |
|118	|N2HET1[10]				|OTHER\_HW\_POWER\_OFF  |OD|Power off the other board |
|119	|ECLK					|UMBILICAL\_ATTACHED	|ID|PC104 pin |
|120	|VCCIO					|						|  | |
|121	|VSS					|						|  | |
|122	|VSS					|						|  | |
|123	|VCC					|						|  | |
|124	|H2HET1[12]				|POW\_MEAS\_EN			|OD|\*TX power measurement enable |
|125	|H2HET1[14]				|PA\_PWR\_ON			|OD|Enable PA power |
|126	|GIOB[0]				|AX5043\_IRQ\_RX2		|ID|Interrupt from AX5043 RX2 |
|127	|N2HET1[30]				|						| D|free gpio|
|128	|CAN2TX					|CAN\_B\_TX				|OU|CAN bus B transmit |
|129	|CAN2RX					|CAN\_B\_RX				|IU|CAN bus B receive |
|130	|MIBSPI1NCS[1]			|\*FEED\_WATCHDOG		|OU|Resets the hardware watchdog timer |
|131	|LINRX					|UART\_RX2				|IU|PC104 Pin 36 |
|132	|LINTX					|UART\_TX2				|OU|PC104 Pin 32 |
|133	|GIOB[1]				|ACTIVE\_N				|BD|Local active pin for active/standby |
|134	|VCCP					|						|  | |
|135	|VSS					|						|  | |
|136	|VCCIO					|						|  | |
|137	|VCC					|						|  | |
|138	|VSS					|						|  | |
|139	|N2HET1[16]				|						| D|free gpio|
|140	|N2HET1[18]				|						| D|free gpio|
|141	|N2HET1[20]				|AX5043\_PWR\_EN		|OD|Main power enable for all AX5043s |
|142	|GIOB[2]				|AX5043\_IRQ\_TX		|ID|Interrupt from AX5043 TX |
|143	|VCC					|						|  | |
|144	|VSS					|						|  | |

\*Notes below

Interrupts and GPIOs
--------------------

On the TMS570, most normal pins can also be used at GPIOs, but they
are not capable of generating interrupts.  Only the GIOx[n] pins can
generate interrupts, and they are all used for that purpose.

Notes on thermsistors
---------------------

Thermsistors are connected to ADC pins on the processor to measure
temperatures on the board.  Resistance varies from 534 ohms (125C) to
188.5K (-40C).  There is a 10K bias, so this gives this gives a .17V
(125C) to 3.13V (-40C) voltage range.  It is supposed to be fairly
linear.

Notes on Processor\_Reset
------------------------

The 3.3V and 1.2V power converts have power good output pins, and the
1.2V current limiter has a power good pin, all open collector.  These
are wire-or-ed to the processor reset pin.  When any of them senses
there is a power issue, they will pull the reset pin.  After the 1.2V
current limiter turns on (which takes a little bit of time, it is
inrush limited) it will wait 50us and before releasing the reset pin,
so reset should happen automatically on any power up or power problem.

Notes on FEED\_WATCHDOG
-----------------------

This must be toggled at least once a second.  If it isn't, the
hardware watchdog will power off the board for 200ms and power it back
on.

Notes on TX Power Measurement
-----------------------------

A directional coupler and power measurement chips (ADL5501AK) feed
into the ADCs (Forward power to pin 74 AD1IN[3] and reverse to pin 73
AS1IN[2]) and an enable for those parts into pin 124 N2HET1[12].  Pin
124 is pulled down by default, so the chips will be disabled at reset.
The direction coupler is 4mm long with .1524mm traces .127mm apart.
At full power out (+33dBm) this will result in about -7dBm of power
from the coupler.  This was simulated with a transmission line in
qucs.  The voltage for that can be calculated from the chip manual.

FIXME - Figure out what all the PC104 pins do.

# PC104 Pins

  - HW\_POWER\_OFF[12]\_N - Input to board, pulling this low causes the
    power to be disabled on boardn.  boardn pulls this high with a 10K
	resistor.  If driven, it should be open drain or open collector.
	Be careful not to glitch this line.

  - PRESENCE[12]\_N - The board is physically present.  This must be
	pulled high by a 1M resistor on entity reading this value, it is
	pulled low by a 10K resistor on boardn.
	
  - ACTIVE[12]\_N - boardn is asserting that it is active.  This is
	pulled high on boardn and will be driven low by boardn when it is
	active and not under external active/standby control.  When under
	external active/standby control, this is an input that another
	entity must pull low to cause the board to go active.
	
  - FAULT[12]\_N - Output from boardn, the processor is reporting an error.

  - UMBILICAL\_ATTACHED - Input to the board, if high the satellite is in
    the launch vehicle.  This inhibits transmit in hardware and causes
	the software to behave differently.  If this line is not used make
	sure to populate the resistor pulling it down.
	
  - SAFE\_MODE\_N - Connected to the processor so a controlling system
    can tell it to go into a safe mode.  What it does depends on context.

  - 5V_p - +5V that is always present when the satellite is powered.
    The board has a 0 ohm resistor that must be populated to get power
	from these pins.
  
  - 3V3_p - +3.3V that is always present when the satellite is powered.
    The board has a 0 ohm resistor that must be populated to get power
	from these pins.
  
  - 5V_S[1-3] - Switched +5V power from the power supply.  The board
    has 0 ohm resistors, one of which must be populated to get power
    from these pins.
  
  - 3V3_S[1-3] - Switched +3.3V power from the power supply.    The
	board has a 0 ohm resistor that must be populated to get power
	from these pins.

  - I2C\_SDA, I2C\_SCL - I2C bus pins

  - GND
  
  - CAN[AB][+-] - CAN bus signals.
  
# Active/Standby Configuration

The boards supports having a mate board that is the same board with
one resistor difference to differentiate between board 1 and board 2.
The BOARD\_NUM line is used to tell which board you are.  This also
selects values coming from the PC104.  The "other" board is the board
you are not.  The lines on the PC104 are:

- PRESENCEn\_N - This is used to tell if the other board is present
  (even if it is powered down).  It will be high if not present and
  low if present.
  
- FAULTn\_N - This is used to tell if the other board has had a fault
  and is failing.  This board can take over processing at that point.
  
- ACTIVEn\_N - Used to tell which board is active.  The board that is
  asserting its line thinks it is active.  If both boards assert this,
  board 1 will be active and board 2 must deactivate.
  
- HW\_POWER\_OFFn\_N - Used to power the other board off.  It this
  board thinks the other board is misbehaving, it can power off the
  other board.

The lines from the other board become OTHER\_PRESENCE\_N,
OTHER\_FAULT\_N, OTHER\_ACTIVE\_N, and OTHER\_HW\_POWER\_OFF\_N on a
board.  The lines for this board become PRESENCE\_N, FAULT\_N,
ACTIVE\_N, and HW\_POWER\_OFF\_N.

The active board may also be externally controlled.  If the
EXTERN\_CONTROL line is pulled high, the board will assume that some
other external entity will choose which board is active.  In this
case, the ACTIVE\_N line becomes an input and the processor monitors
that line to know if it should be active or not.

The ACTIVE1\_N line also controls several RF switches on board 1.
There is a second set of SMA connectors that connect from board 1 to
board 2 to carry the RF to board 2.  If board 1 is active, the RF is
switched to board 1 and the RF to/from board 2 is shunted to a 50 ohm
resistor between transmit and receive.  Likewise, when board 1 is
inactive, it connects the RF to the board 2 connectors and shunts the
board 1 RF between transmit and receive through a 50 ohm resistor.
(For the reason for this shunt, see the section on RF Loopback Test)

On board 2, the RF switches are not populated and the RF goes through
a zero ohm resistor to connect it, bypassing the switch connections.
On board 1 these resistors must not be populated.  If the board is
configured for simplex, then the RF switches are also not connected
and the zero ohm resistors are populated.

It is also possible to have separate antennas for each board.  Then
the RF switches and second set of SMAs are not relevant and can be
removed or just set up for loopback testing.

All the board switch circuitry is powered with +5V so it works even if
the board is powered down.  Care must be taken to not drive any I/O
lines with +5V; voltage dividers are present in several places to
bring +5V down to +2.5V for pull ups.

See the end of this document for the active/standby state machine.

MRAM data is automatically synced to the other board via the CAN bus.
The inactive side has the MRAM unmounted and is only syncing data.
The sync protocol is reliable and the remote end must respond that it
has written the data before the local end commits the write.  When a
board activates, it mounts MRAM and continues operation.  Applications
can either store all state data in MRAM or they can implement their
own synchronization protocol.

When the other board is down and then comes up, it will request a full
sync and all data will be transferred.  On a requested activity
switch, special handling is done to keep both sides in sync so the
newly inactive side can simply start receiving updates and a full sync
is not required.

If the inactive board detects a sync error, it will request a full
sync.

The inactive board will have all RF powered down and will do minimal
processing to avoid using very much power.  Basically just handling
synchronization data.

# RF Loopback Test

When in standby mode, the inactive board will have the RF output of
the transmitter tied in to the RF input of the receiver through a 50
ohm resistor.  At 440MHz, the input impedance of the first receive
filter is very low and its gain at 440MHz is <-100dB.  So it should
be safe for both the transmitter and receiver if the transmitter
transmits at 440MHz at full power.

If the transmitter transmits at 144.5MHz, the calculated loss in all
the filters is around -75dB.  There is 20dB of gain in the PA, and the
AX5043 can send at 16dBm.  Adding all that up, you get -39dBm coming
out of the transmitter.  If that is sent through the 50 ohm resistor,
there will be some more loss there, but you should get a signal well
within readable range for the receive AX5043s.  And though the
mismatch will be bad for the transmitter, the power is low enough to
not harm the PA.  So this can be used as a self test of the
transmitter and receiver while the board is in inactive mode.  If the
signal too hot, the transmit AX5043 can reduce output power.

If populated with the proper RF switches (the ones hooked to
BOARD1\_RF\_IN\_BYPASS), this could be done on a simplex board, too.
It can just deactivate its ACTIVE\_N line and the RF switch will go to
the bypass.

I am unsure if the TX AX5043 can be coerced into being able to
transmit at both 144MHz and 440MHz.

# Power Control and Sequencing

The power control on the board is fairly simple.  On power up, power
comes in through VSYS, goes through and inductor, and goes to +5V,
which is always powered on.  +5V goes through a current limiter to
+5VAL, which power the circuits on the board that are always on, the
circuits the handle the board presence/active/etc. and the board1 RF
switches, and the CAN bus transceivers.  3.3V comes in to REG\_3V3
from the bus.

The TPSM828302ARDSR will start supplying 1.2V to REG\_1V2.  It will
also pull the PROCESSOR\_RESET pin low until their power is good, and
that point they will not pull the reset line low any more (they are
open drain).  At that point the MP5073GG-P is also holding reset line
low until it is enabled.  Since the MP5073GG-P is powered by REG\_3V3
it will not let the reset line go until that power is good.

The STWD100NYWY3F hardware watchdog will power up at that time, but
the POWER\_ENABLE pin from it will be pulled high and should remain
high for 1 second.

The MP5073GG-P and MAX4495AAUT current limiting chips will start
supplying power to the rest of the board once they detect that power
is good.  However, the MP5073GG-P will wait 50us after it senses the
1.2V power is good holding the PROCESSOR\_RESET line low, then it will
let the processor go.

All the chips driving the PROCESSOR\_RESET line have power sensors, if
any of them sense that the power is bad they will pull that line down
low.

When the processor is in reset and the default settings on the
PA\_PWR\_EN, AX5043\_PWR\_EN, and LNA\_ENABLE are pulled low (and
they have pull downs, too, so that they are disabled even when the
main power is disabled), so all power to the RF elements will be
off.

A HW\_POWER\_OFF\_N comes in from the PC104 connector; if that is
pulled low it will power off everything on the board except for the
devices on +5VAL.  It does this by disabling the 3.3V and 1.2V
regulators.  When 3.3V is off, the MAX4995s controlling power to the
PA, AX5043s, and LNA will be powered off.

There is also a hardware watchdog, as mentioned before.  The processor
must toggle the FEED\_WATCHDOG line at least once a second.  If it
fails to do that, the 1.2V and 3.3V current limiters will be disabled
cutting power to the processor and all digital components.  This will
result in everything else being powered off (except the devices on
+5VAL).  After 200ms, the watchdog chip will enable power again.

To power up and enable the RF section, the processor must first make
sure all the AX5043 enable lines are pulled high to disable them.
This is not the default (some are low and some are high by default),
but it doesn't matter because they are powered off at the main,
anyway.  The processor then can drive AX5043\_PWR\_EN high to enable
the power to all AX5043s.  The processor can then drive the individual
AX5043 enables low to individually power them on.  Then the processor
can drive PA\_PWR\_EN high to power on the PA and LNA\_ENABLE high
to power on the LNA.

# Board Configuration

The board has a number of resistors for configuration.  These are:

  - 1.2V\_INPUT - Determines whether 1.2V is derived from 3.3V or 5V.

  - BOARD\_NUM - Remove for board 1 or simplex, populate for board 2.

  - EXTERN\_CONTROL - Remove if the board (or board pair) manage their
    own activity and power state.  Populate if another entity controls
    power and the active lines on a board pair.  This should generally
    not be populated on a simplex board, it will always be active and
    some other entity probably controls its power signal.
	
  - 5V\_S[1-3], 5V\_p - One of these should be populated depending on
    where the board should get its +5V power.

  - 3V3\_S[1-3], 3V3\_p - One of these should be populated depending on
    where the board should get its +3.3V power.  In addition, there is
	an optional buck regulator that can be populated to derive 3.3V
	from 5V.

  - RF\_SWITCH\_EN - Removing the resistor to +5AL will disable all
    the RF switches into high impedance mode.  Then the zero ohm
    resistors to bypass the switches can be added.

  - UMIBLICAL\_ATTACHED - If this line is not externally used, the
    resistor from this to ground must be populated.

In addition, for simplex, or if each board in a two-board set has its
own antenna connections or antennas, all the chips and resistors on
the RF Output Switch and RF Input Switch schematic pages can be
removed, the zero-ohm resistor between RF\_OUT\_SWITCH and "TX ANT
OUT" can be added, and the zero-ohm resistor between RF\_IN\_SWITCH
and "RX ANT IN" be added to remove all the RF switching.

To completely remove active-standby, in addition to the previous
paragraph, all the parts and resistor and the Active Standby Config
page can be removed and the zero-ohm resistor between
HW\_POWER\_OFF1\_N and HW\_POWER\_OFF\_N added for external power
control of the board.

The power output measurement circuitry on the RF\_Power\_AMP\_FET page
can be removed if output or reflected power measurements are not
necessary.

# Active/Standby State Machine

The logic below is for the board being active or not.  For instance,
if OTHER\_FAULT\_N is low, then it is true.  These are all this way
since they are all negative logic.  This is only used if the active
state is not externally controlled.

The boards will switch activity periodically to test the other board.

  - PowerUp:

    - !OTHER\_PRESENCE\_N -> ActiveOtherBoardNotPresent
    - OTHER\_PRESENCE\_N && OTHER\_ACTIVE\_N -> Inactive
    - OTHER\_PRESENCE\_N && !OTHER\_ACTIVE\_N && !IAmBoard2 -> ActiveOtherBoardPresent
    - OTHER\_PRESENCE\_N && !OTHER\_ACTIVE\_N && IAmBoard2 -> InactiveWaitActivate
      - start timer

  - Inactive:
    - OTHER\_FAULT\_N -> ActiveOtherBoardPresent
      - power cycle other board.
    - !OTHER\_ACTIVE\_N -> ActiveOtherBoardPresent
    - !OTHER\_PRESENCE\_N -> ActiveOtherBoardNotPresent
      - log presence issue

  - InactiveWaitActivate:
    - OTHER\_FAULT\_N -> ActiveOtherBoardPresent
      - stop timer
      - power cycle other board.
    - OTHER\_ACTIVE\_N -> Inactive
      - stop timer
    - !OTHER\_ACTIVE\_N && timeout -> ActiveOtherBoardPresent
    - !OTHER\_PRESENCE\_N -> ActiveOtherBoardNotPresent
      - stop timer
      - log presence issue

  - ActiveOtherBoardPresent:
    - OTHER\_FAULT\_N -> ActiveOtherBoardPresent
      - power cycle other board.
    - OTHER\_ACTIVE\_N -> Inactive
    - !OTHER\_PRESENCE\_N -> ActiveOtherBoardNotPresent
      - log presence issue
  
  - ActiveOtherBoardNotPresent:
    - OTHER\_PRESENCE\_N -> ActiveOtherBoardPresent
      - log presence issue

Note that except for power up, transitions based on OTHER\_PRESENCE\_N
should never happen.  These should be logged.

FIXME - There needs to be some synchronization handling added to this.

FIXME - Some sort of handling needs to be added in the case that the
other board is determined to be faulty.

FIXME - May need to debounce some of these lines.

FIXME - For a controlled activity switch, it probably needs to be
handled by messaging and the hardware lines are used to do the final
switch.

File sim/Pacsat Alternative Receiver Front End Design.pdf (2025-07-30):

Pacsat Alternative Receiver Front End Design

Jim McCullers – WA4CWI

The following, for consideration, is a proposal for an alternative to the current Pacsat four-receiver configuration that reduces build cost, gains valuable board space and reduces weight without loss of performance.

Background

Pacsat requires four receivers operating on different frequencies within a common frequency range. The receivers share a common antenna, LNA and filtering. The output of the final component in the commonly shared chain must be split into four matching connections without substantial performance losses incorporating impedance matching for the individual receivers. The 1”4 split introduces a minimum 6db loss which must be overcome by the shared LNA.

Pacsat uses OnSemi AX5043 devices as receivers. The AX5043 has an uncommon receiver input requirement as a result of allowing as an option both receive and transmit on the same chip interface. The AX5043 incorporates an internal Class E amplifier which requires an output consisting of a 180-degree phase differential connection. The receiver, using the same connection, expects a 180-degree differential input.

The prototype Pacsat board uses a combination of a center tapped RF transformer as a 1:2 splitter with each output leg feeding a 1:4 transformer to obtain the necessary isolate 180-degree phase differential input to each of the four AX5043 receivers.

Analysis

The basic shared receiver-transmitter interface shown in Attachment 1 is similar to Figure 14 of the AX5043 Datasheet (Page 37). Looking from left to right there are three components, low pass filter, phase balun and transmitter Class E tank. The phase balun consists of a commonly fed inductor-capacitor low pass and high pass filter each feeding a leg of the AX5043 differential input/output. The low and high pass filter introduce a 90-degree phase shift in the opposite direction, the end result being a 180-degree differential connection to the AX5043. The phase balun must be tuned to the center frequency for the device.

Attachment 2, based on Figure 15 of the AX5043 Datasheet (Page 38), shows a configuration where the output of the AX5043 on transmit is taken from the optional PA output (not shown) and the receiver fed through a single ended circuit consisting of a blocking capacitor and the high-low pass balun into the receiver differential input. The AX5043 receiver requires an inductor to ground on each leg of the differential input. One of these conditions is met by the grounded inductor of the high pass filter with an additional inductor attached to the low-pass fed leg to ground.

During the early days of Pacsat development a Jonathan Brandenberg receiver board was modified to test this configuration on a single receiver with no obvious loss in performance. However, no formal performance testing was performed.

Proposal

It is proposed the three-transformer arrangement of the prototype Pacsat board be replaced with a single 1:4 splitter transformer with each output of the transformer forming a single ended input through individual phase baluns to the AX5043 differential receiver input.

As the necessary components are common inductors and capacitors with no power handling requirements, using this approach will result in eliminating transformer cost in addition to reducing board weight and regaining board space for other features. This approach will require a new board layout requiring increased board area for each receiver.

Calculators to determine the component values for the phase baluns can be found on the internet. The values for the components in the AX5043 Datasheet indicate they are designed for reference frequency of 169mhz. However, when values are calculated for 169mhz using several available calculators, the values do not match those in the AX5043 Datasheet. Therefore, some work is needed to resolve this difference. It would be easy to construct a small board using calculated components to test the phase output as verification.

It is also assumed that the phase balun for each of the four receivers will be set to a common center frequency unless testing indicates a wide variation in output phase requiring separate phase balun component values for each receiver.

If proof of concept testing is desired, the LaunchPad board could be redone to accommodate two receivers using a 1:2 splitter which would result in a 3db signal loss rather than the 6db loss incurred by a 1:4 splitter. To emulate the performance of a four-receiver configuration a 3db attenuator would be added to the receive path prior to the splitter. The bandpass filter and LNA from the Pacsat prototype board should be included for full path testing.

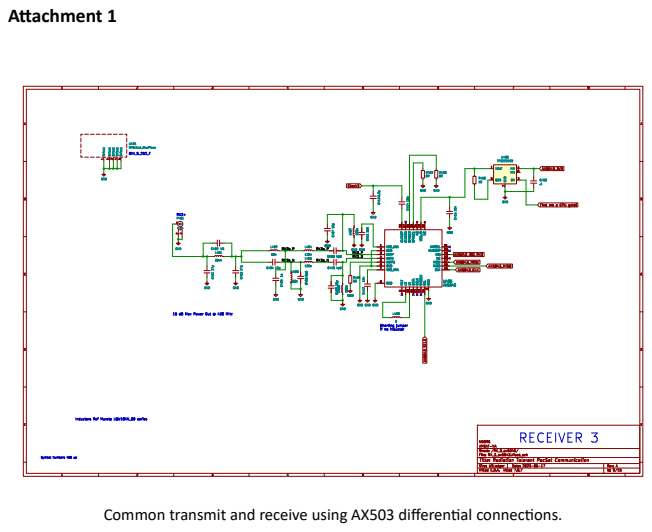
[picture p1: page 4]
Attachment 1

Common transmit and receive using AX503 differential connections.

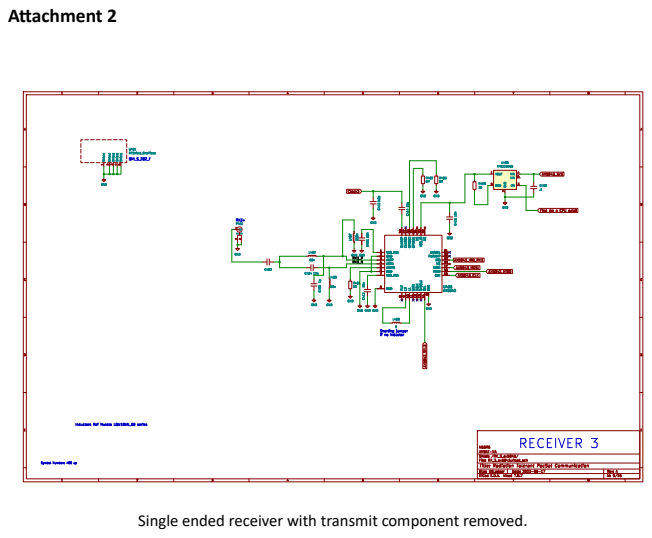
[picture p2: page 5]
Attachment 2

Single ended receiver with transmit component removed.

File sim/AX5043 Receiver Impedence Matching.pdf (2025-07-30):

AX5043 Receiver Impedence Matching

Jim McCullers - WA4CWI

Preliminary

The AX5043 is a versatile RF transceiver for digital modulation within a frequency range of 27 to 1050 mhz. Modulation modes are: FSK/MSK/4−FSK/GFSK/GMSK/ASK/AFSK/FM/PSK.

Impedance matching and bandpass filtering are necessary for proper operation. Transmission and reception are supported via a differential interface with an additional single-ended transmission option on a separate pin. All reception must utilize the differential option.

The classic transmit/receive differential circuit from the AX5043 data sheet is:

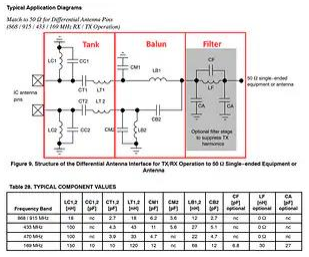
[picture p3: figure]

As shown in the circuit schematic the matching/filtering circuit can be divided into three sections, Filter, Balun and Tank. The Filter section is a low-pass filter for VHF and omitted in UHF versions. The Tank portion of the schematic is designed to match the needs of the AX5043 Class E power amplifier and can be eliminated for a receive only design with a reduction in components and printed circuit board space. The Balun serves to convert between the AX5043 differential interface and a single ended connection.

Component values presented in the datasheet for VHF are above the frequency range for amateur radio. To explore the design and performance of a reduced component receive only circuit for amateur radio satellite reception, a receive only design was prototyped and tested for the 2-Meter amateur radio band (144-148 mhz) consisting of only the Balun circuit. Calculations were performed using 146mhz as the target frequency.

A balun is an impedance matching device between balanced and unbalanced. As the AX5043 requires a differential interface, the balun is used to convert the single ended RF connection to the required differential termination. The balun circuit presented in the AX5043 circuit is a lumped element design comprising capacitors and inductors. Examining the circuit shows it to be a low-pass/high-pass filter at the designed center frequency which functions as a phase splitter, delivering the required differential signal (180 degree phase shift).

There are several lumped element balun calculators available on the internet. For this experiment the calculator at http:// http://leleivre.com/rf_lcbalun.html was used to calculate the values needed for a balun centered at 146 mhz.

The AX5043 is very broad band and no impedance values are given in the product data sheet. Therefore a impedance of 100 ohms was used as the target value for the differential input which gave similar results when the input frequency to the calculator was 169 mhz as charted in the data sheet. For a 146 mhz frequency the calculated values were 15.42 pf capacitance and 77 nh inductance.

The AX5043 has an additional requirement in that both sides of the differential input must show a DC path to ground. The AX5043 data sheet circuit utilizes the inductors of the Class E tank circuit to achieve this requirement. For a receive only circuit consisting of the balun section an additional inductor is required on the low-pass side of the balun.

Simulations were performed on the balun circuit using 1nh as the additional DC path inductor as a 1nh value is the lowest SMD component value available.

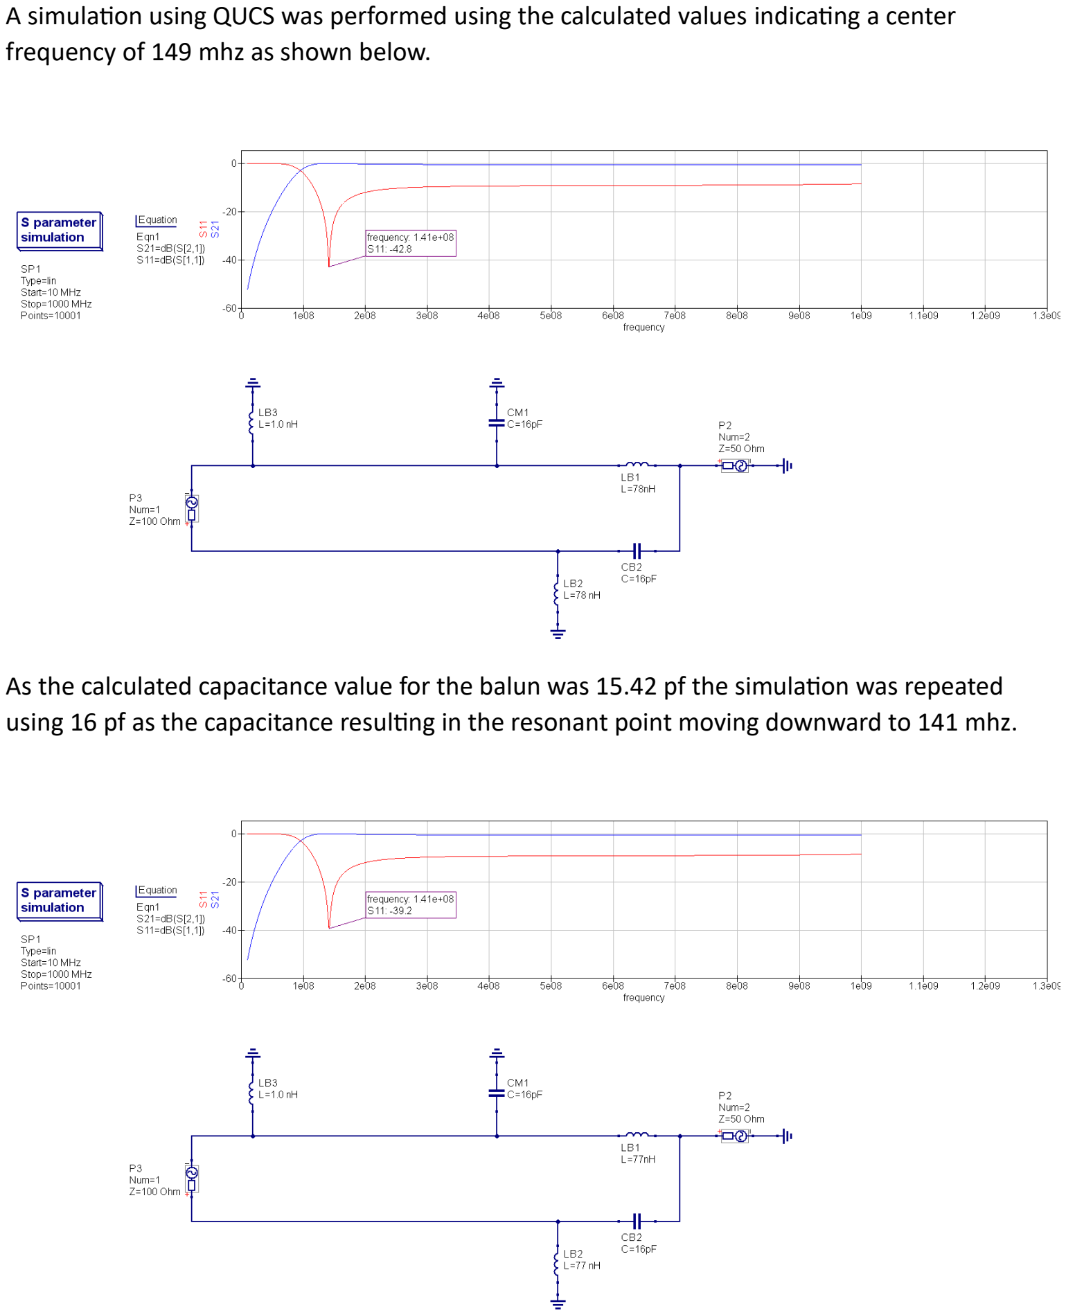
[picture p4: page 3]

A simulation using QUCS was performed using the calculated values indicating a center frequency of 149 mhz as shown below.

As the calculated capacitance value for the balun was 15.42 pf the simulation was repeated using 16 pf as the capacitance resulting in the resonant point moving downward to 141 mhz.

For testing, a DigitalTxRxRpi board was modified using jumpers to eliminate the low pass filter and Class E tank circuit and a 100 ohm resistor substituting for the AX5043 differential input. Available values near the calculated/simulated values were used with the capacitance being 15 pf, balun inductors 78 nh and the DC inductor 1.0 nh. This moved the simulated resonant point to 149 mhz.

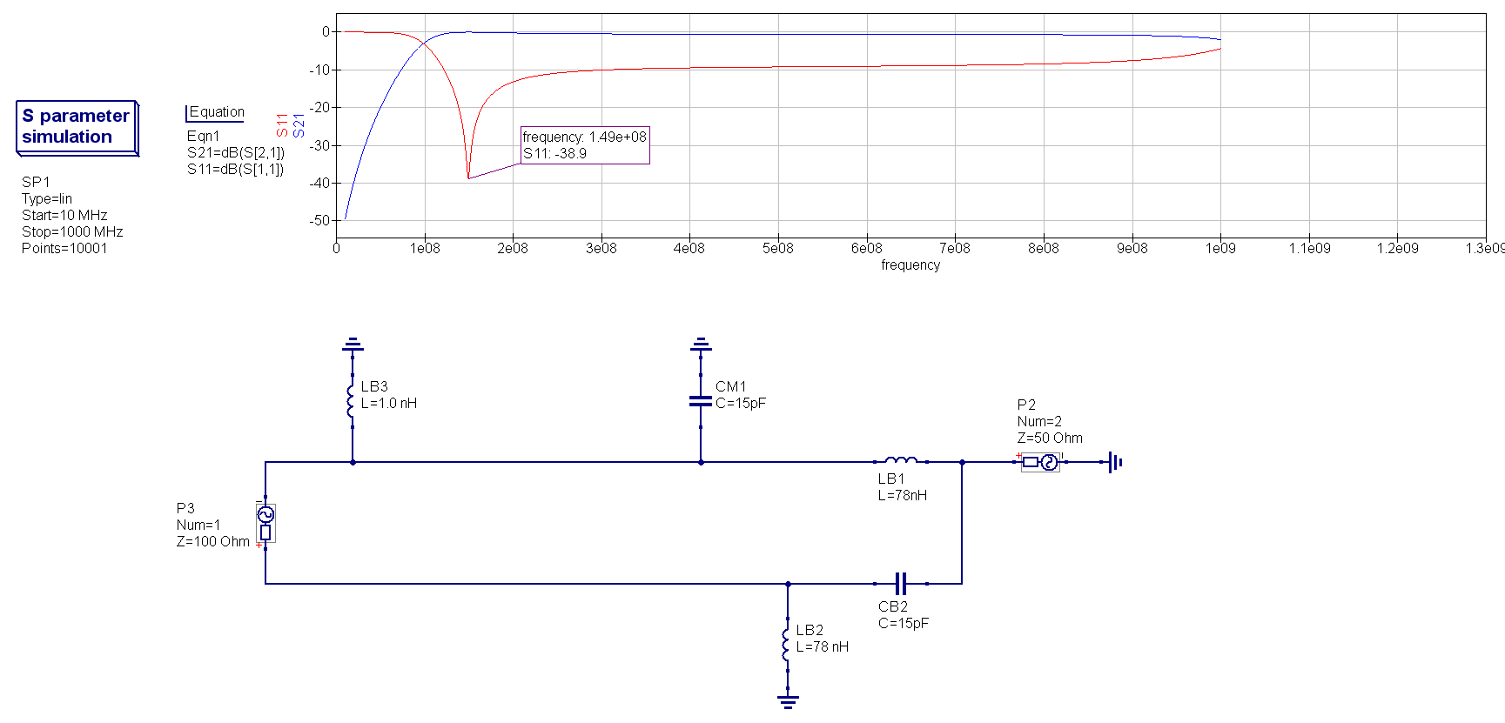
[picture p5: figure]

Additional simulations showed the DC path inductor had minimal impact on the resonant cross point frequency but the lowest possible value is recommended.

Measuring the built circuit showed similar results with differences from the simulated design attributed to PCB stray capacitance/inductive interactions.

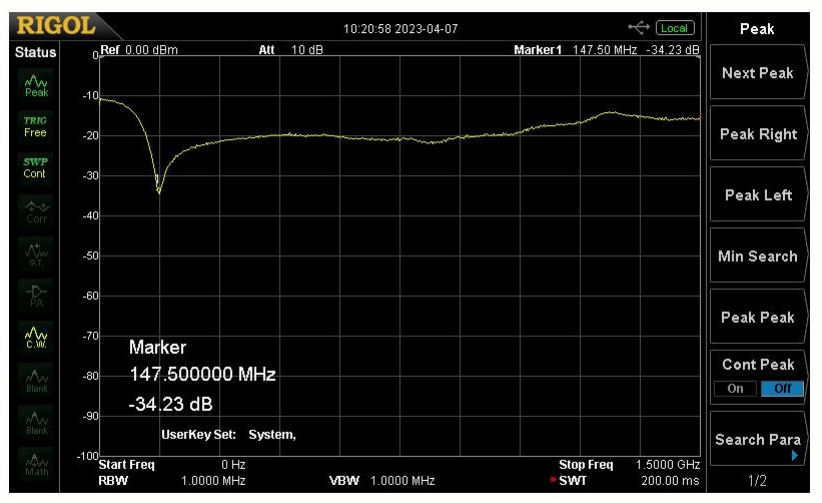
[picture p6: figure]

Wide Trace 0 – 1.5 ghz

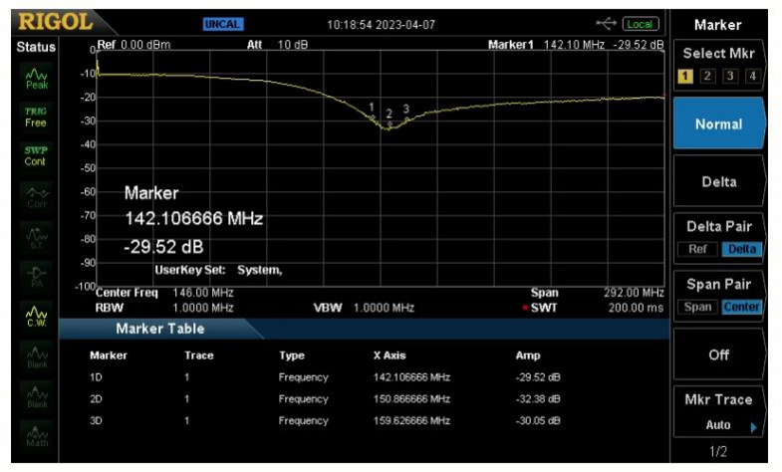
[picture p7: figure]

3db Trace

The 100 ohm resistor was removed and the DigitalRxTxRPi circuit completed to allow for real world testing. The low-pass filter from the original circuit was installed to match a complete TxRx VHF board available.

Using 144.39 mhz 1200 baud AFSK APRS as the test source no appreciable difference was noticed between the complete TxRx board and the reduced receive only board in signal level (RSSI) and decoded APRS packets.

Summary

The AX5043 requires a differential RF interface where each side of the differential must include a DC ground path. This is accomplished in a full Tx/Rx design by using inductors that comprise the Class E amplifier tank circuit.

A smaller receive only design can be accomplished by eliminating the Class E tank circuit, utilizing the balun section only tuned to the desired center frequency with a small value inductor to ground as the required DC path.

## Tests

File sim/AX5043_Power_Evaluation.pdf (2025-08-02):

AX5043 Power Study

A power requirements study was performed on a AX5043 transceiver chip to verify the power required matched vendor specification.

The AX5043 was tested using a modified DigitalTxRxRPi board created by Jonathan Brandenburg employing a Raspberry Pi 4 as the host. Modifications were the removal of the power indicator LED to eliminate that power requirement. It was easier given the design of the board to measure the current at the +3.3 header pin. The board trace was cut at the header and a Fluke 187 multi-meter inserted for current measurement in milliamps.

Frequency was set to 435.3 MHz with a steady carrier. Output from the output SMA connector was coupled to a 3db attenuator, then through two cables and one bridge connector to the input of a Rigol DSA815 Spectrum Analyzer. The measured loss of the attenuator and cable was 3.1 db which was added to the value indicated by the SA to obtain the output power during transmit.

Testing was performed at approximately +16, +10 and 0 dB output with the following results.

Transmitter Output (dBm) | Measured Current (mA)
15.74 | 56.58
10.19 | 30.77
0.6 | 14.7

Power requirements were determined to be within the manufacture’s specifications.

The DigitalTxRxRPi board is configured as a differential output PA. According to the manufacture, a single ended configuration results in an approximate 1.5 dB reduction in output power at a reduction of approximately 20 mA power requirement.

Following the transmitter power test the receiver power requirement was evaluated which initially resulted in +17 mA more than the manufacture specification. After extensive debugging it was determined the addition power was the result of the AX-Radio Lab configuration output that defaulted the Data and Data Clock pins to a high state which were coupled by the board to circuits on the host Pi. Setting both the Data and Data Clock pins low in the configuration (registers PINFUNCDCLK and PINFUNCDATA) eliminated the excess current demand.

The receiver current draw was measured in five steps by altering the AX5043 PWRMODE register.

Power State | Measured Current (mA)
Idle | .478
Power Down | .177
Crystal Oscillator enabled | .637
Synthesizer running, Receive Mode | 6.34
Receiver Running | 10.95

The manufacture specification is 9.5 mA at 433 MHz. Therefore the measured current is within reasonable range.

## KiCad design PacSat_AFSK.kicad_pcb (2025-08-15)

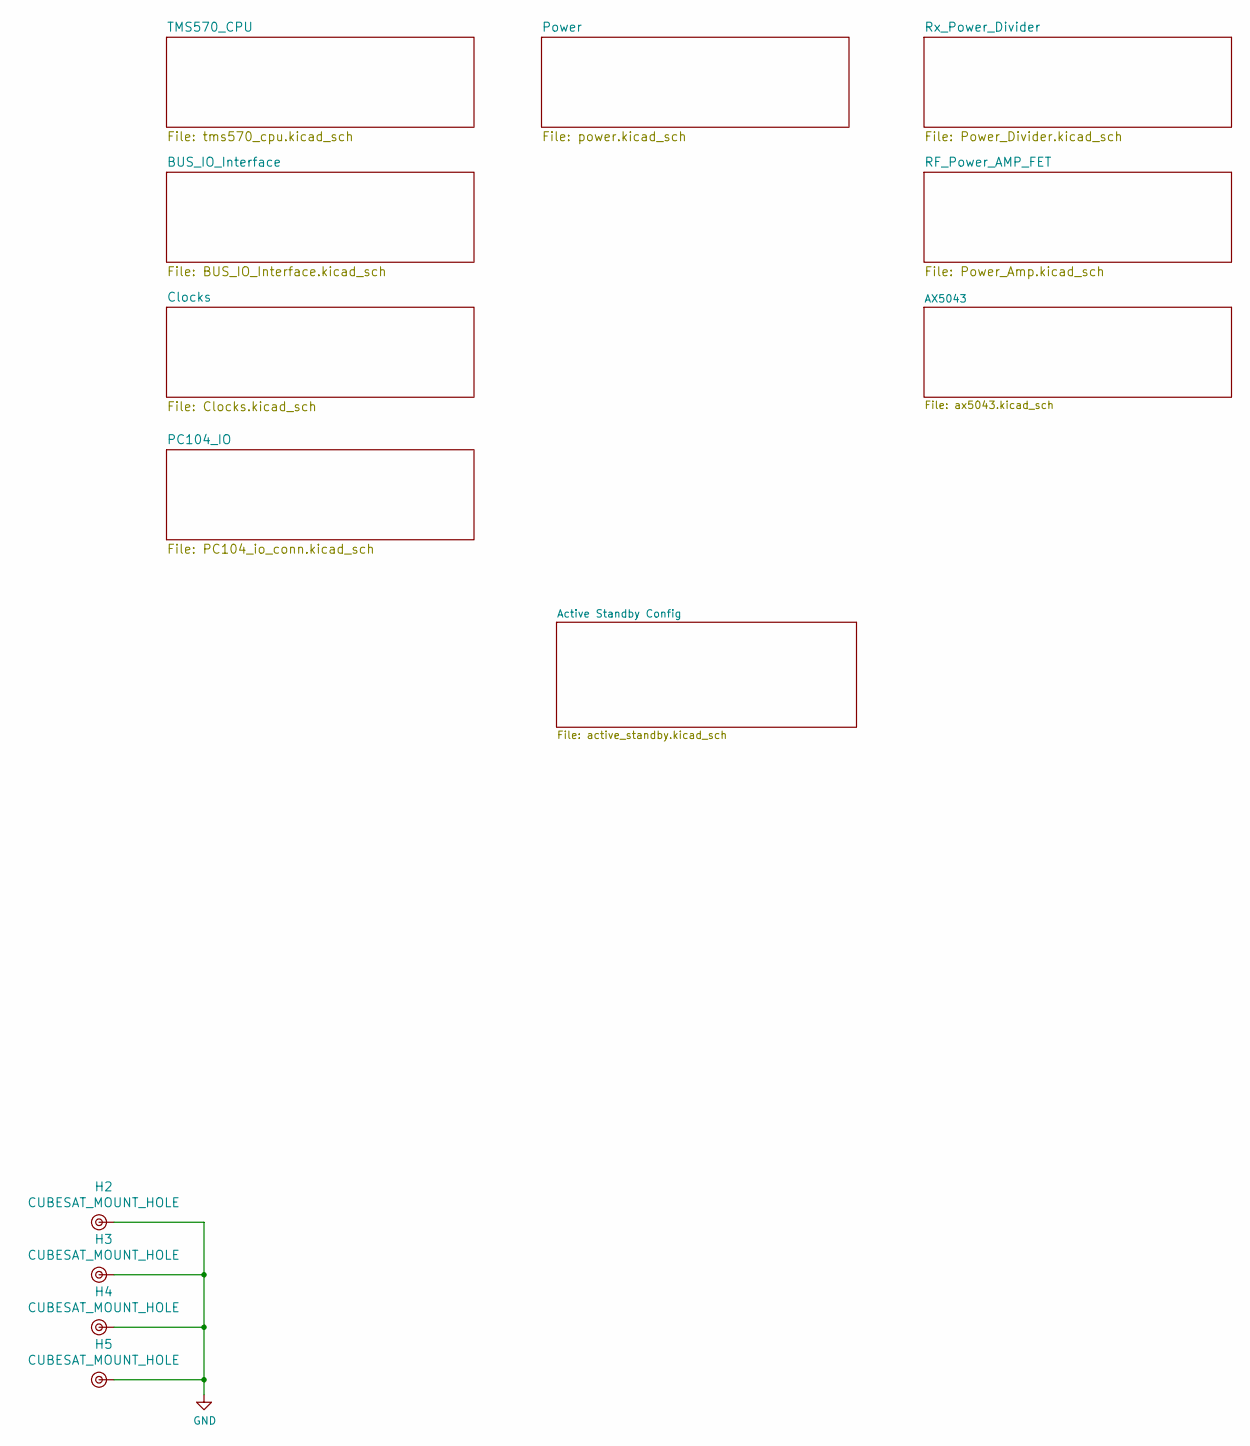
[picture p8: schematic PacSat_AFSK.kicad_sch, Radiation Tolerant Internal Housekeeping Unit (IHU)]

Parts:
H2, H3, H4, H5: CUBESAT_MOUNT_HOLE

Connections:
GND: H2.1, H3.1, H4.1, H5.1; also elsewhere on the board

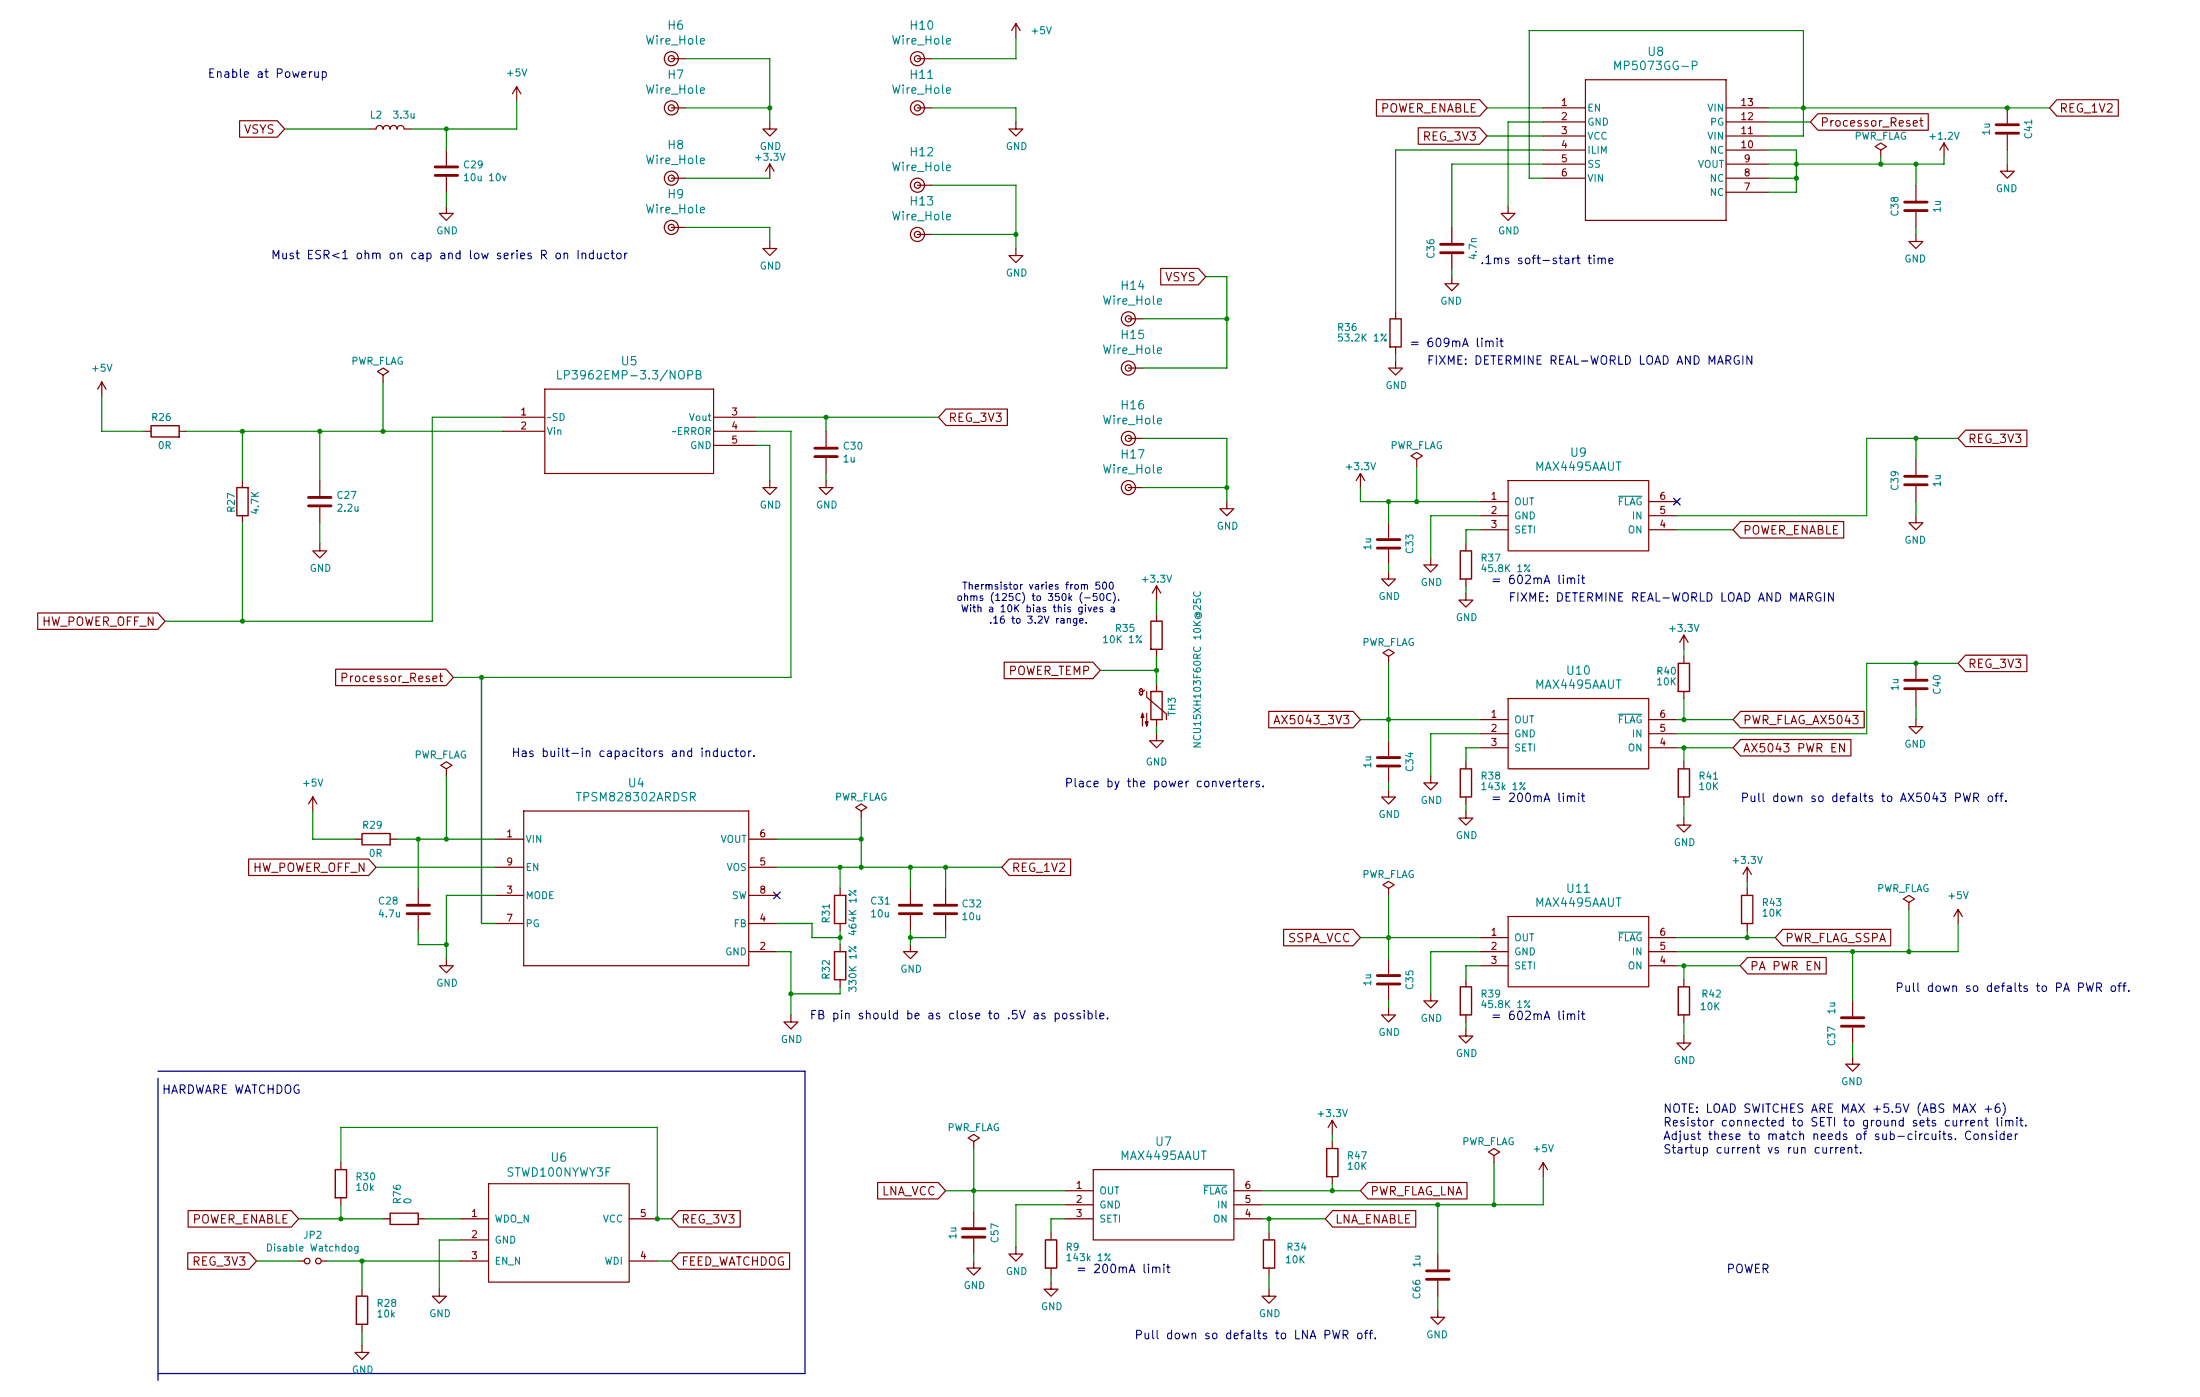
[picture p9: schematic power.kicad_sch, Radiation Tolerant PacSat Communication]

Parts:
C27: 2.2u; C_0805_2012Metric_Pad1.18x1.45mm_HandSolder
C28: 4.7u; C_0805_2012Metric_Pad1.18x1.45mm_HandSolder
C29: 10u 10v; C_1206_3216Metric
C30, C33, C34, C35, C37, C38, C39, C40, C41, C57, C66: 1u; C_0805_2012Metric_Pad1.18x1.45mm_HandSolder
C31, C32: 10u; C_0805_2012Metric_Pad1.18x1.45mm_HandSolder
C36: 4.7n; C_0603_1608Metric_Pad1.08x0.95mm_HandSolder
H6, H7, H8, H9, H10, H11, H12, H13, H14, H15, H16, H17: Wire_Hole
JP2: Disable Watchdog; SolderJumper-2_P1.3mm_Open_RoundedPad1.0x1.5mm
L2: 3.3u; L_1210_3225Metric_Pad1.42x2.65mm_HandSolder
R9, R38: 143k 1%; R_0603_1608Metric_Pad0.98x0.95mm_HandSolder
R26, R29: 0R; R_0603_1608Metric_Pad0.98x0.95mm_HandSolder
R27: 4.7K; R_0603_1608Metric_Pad0.98x0.95mm_HandSolder
R28, R30: 10k; R_0603_1608Metric_Pad0.98x0.95mm_HandSolder
R31: 464K 1%; R_0603_1608Metric_Pad0.98x0.95mm_HandSolder
R32: 330K 1%; R_0603_1608Metric_Pad0.98x0.95mm_HandSolder
R34, R40, R41, R42, R43, R47: 10K; R_0603_1608Metric_Pad0.98x0.95mm_HandSolder
R35: 10K 1%; R_0603_1608Metric_Pad0.98x0.95mm_HandSolder
R36: 53.2K 1%; R_0603_1608Metric_Pad0.98x0.95mm_HandSolder
R37, R39: 45.8K 1%; R_0603_1608Metric_Pad0.98x0.95mm_HandSolder
R76: 0; R_0603_1608Metric_Pad0.98x0.95mm_HandSolder
TH3: NCU15XH103F60RC 10K@25C; R_0402_1005Metric
U4: TPSM828302ARDSR; RDS0009A-MFG
U5: LP3962EMP-3.3/NOPB; MP05A
U6: STWD100NYWY3F; SOT-23-5_HandSoldering
U7, U9, U10, U11: MAX4495AAUT; SOT-23-6_Handsoldering
U8: MP5073GG-P; QFN-12_MP5073_MNP

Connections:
+1.2V: C38.1, U8.7 (NC), U8.8 (NC), U8.9 (VOUT), U8.10 (NC); also elsewhere on the board
+3.3V: C33.1, H8.1, R35.1, R40.1, R43.1, R47.1, U9.1 (OUT); also elsewhere on the board
+5V: C29.1, C37.1, C66.1, H10.1, L2.2, R26.1, R29.1, U7.5 (IN), U11.5 (IN); also elsewhere on the board
AX5043 PWR EN: R41.1, U10.4 (ON); also elsewhere on the board
AX5043_3V3: C34.1, U10.1 (OUT); also elsewhere on the board
FEED_WATCHDOG: U6.4 (WDI); also elsewhere on the board
GND: C27.2, C28.2, C29.2, C30.2, C31.2, C32.2, C33.2, C34.2, C35.2, C36.2, C37.2, C38.2, C39.1, C40.2, C41.2, C57.2, C66.2, H6.1, H7.1, H9.1, H11.1, H12.1, H13.1, H16.1, H17.1, R9.2, R28.2, R32.1, R34.2, R36.2, R37.2, R38.2, R39.2, R41.2, R42.2, TH3.2, U4.2 (GND), U4.3 (MODE), U5.5 (GND), U6.2 (GND), U7.2 (GND), U8.2 (GND), U9.2 (GND), U10.2 (GND), U11.2 (GND); also elsewhere on the board
HW_POWER_OFF_N: R27.1, U4.9 (EN), U5.1 (~SD); also elsewhere on the board
LNA_ENABLE: R34.1, U7.4 (ON); also elsewhere on the board
LNA_VCC: C57.1, U7.1 (OUT); also elsewhere on the board
unnamed: R31.1, R32.2, U4.4 (FB)
unnamed: C28.1, R29.2, U4.1 (VIN)
unnamed: C27.1, R26.2, R27.2, U5.2 (Vin)
unnamed: JP2.2, R28.1, U6.3 (EN_N)
unnamed: R76.2, U6.1 (WDO_N)
unnamed: R9.1, U7.3 (SETI)
unnamed: R36.1, U8.4 (ILIM)
unnamed: C36.1, U8.5 (SS)
unnamed: R37.1, U9.3 (SETI)
unnamed: R38.1, U10.3 (SETI)
unnamed: R39.1, U11.3 (SETI)
PA PWR EN: R42.1, U11.4 (ON); also elsewhere on the board
POWER_ENABLE: R30.2, R76.1, U8.1 (EN), U9.4 (ON)
POWER_TEMP: R35.2, TH3.1; also elsewhere on the board
PWR_FLAG_AX5043: R40.2, U10.6 (~FLAG); also elsewhere on the board
PWR_FLAG_LNA: R47.2, U7.6 (~FLAG); also elsewhere on the board
PWR_FLAG_SSPA: R43.2, U11.6 (~FLAG); also elsewhere on the board
Processor_Reset: U4.7 (PG), U5.4 (~ERROR), U8.12 (PG); also elsewhere on the board
REG_1V2: C31.1, C32.1, C41.1, R31.2, U4.5 (VOS), U4.6 (VOUT), U8.6 (VIN), U8.11 (VIN), U8.13 (VIN)
REG_3V3: C30.1, C39.2, C40.1, JP2.1, R30.1, U5.3 (Vout), U6.5 (VCC), U8.3 (VCC), U9.5 (IN), U10.5 (IN)
SSPA_VCC: C35.1, U11.1 (OUT); also elsewhere on the board
VSYS: H14.1, H15.1, L2.1; also elsewhere on the board

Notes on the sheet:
Has built-in capacitors and inductor.
= 200mA limit
Thermsistor varies from 500 ohms (125C) to 350k (-50C). With a 10K bias this gives a .16 to 3.2V range.
FB pin should be as close to .5V as possible.
FIXME: DETERMINE REAL-WORLD LOAD AND MARGIN
Must ESR<1 ohm on cap and low series R on Inductor
Pull down so defalts to LNA PWR off.
NOTE: LOAD SWITCHES ARE MAX +5.5V (ABS MAX +6) Resistor connected to SETI to ground sets current limit. Adjust these to match needs of sub-circuits. Consider Startup current vs run current.
HARDWARE WATCHDOG
.1ms soft-start time
= 602mA limit
Pull down so defalts to AX5043 PWR off.
Enable at Powerup
Pull down so defalts to PA PWR off.
= 609mA limit
POWER
Place by the power converters.

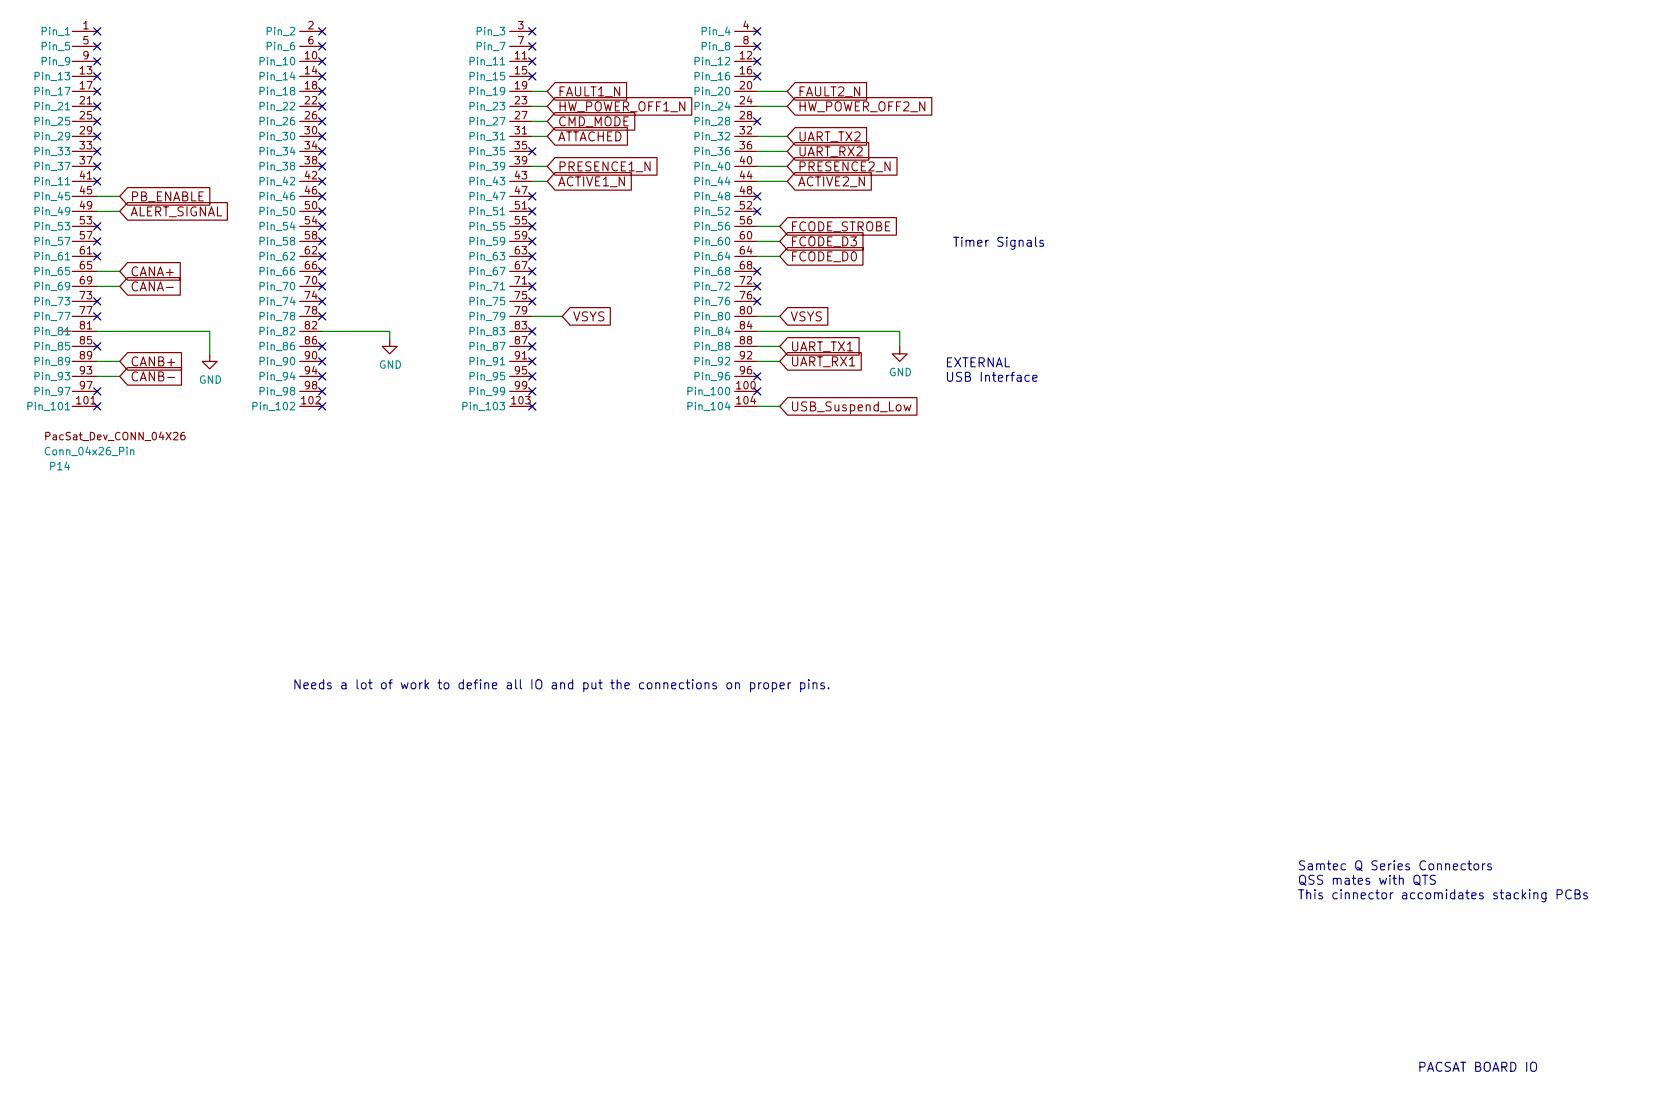
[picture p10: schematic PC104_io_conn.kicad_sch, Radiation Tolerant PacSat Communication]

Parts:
P14: Conn_04x26_Pin; PacSat_Dev_4_26

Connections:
ACTIVE1_N: P14.43; also elsewhere on the board
ACTIVE2_N: P14.44; also elsewhere on the board
ALERT_SIGNAL: P14.49; also elsewhere on the board
ATTACHED: P14.31; also elsewhere on the board
CANA+: P14.65; also elsewhere on the board
CANA-: P14.69; also elsewhere on the board
CANB+: P14.89; also elsewhere on the board
CANB-: P14.93; also elsewhere on the board
CMD_MODE: P14.27; also elsewhere on the board
FAULT1_N: P14.19; also elsewhere on the board
FAULT2_N: P14.20; also elsewhere on the board
FCODE_D0: P14.64; also elsewhere on the board
FCODE_D3: P14.60; also elsewhere on the board
FCODE_STROBE: P14.56; also elsewhere on the board
GND: P14.81, P14.82, P14.84; also elsewhere on the board
HW_POWER_OFF1_N: P14.23; also elsewhere on the board
HW_POWER_OFF2_N: P14.24; also elsewhere on the board
PB_ENABLE: P14.45; also elsewhere on the board
PRESENCE1_N: P14.39; also elsewhere on the board
PRESENCE2_N: P14.40; also elsewhere on the board
UART_RX1: P14.92; also elsewhere on the board
UART_RX2: P14.36; also elsewhere on the board
UART_TX1: P14.88; also elsewhere on the board
UART_TX2: P14.32; also elsewhere on the board
USB_Suspend_Low: P14.104; also elsewhere on the board
VSYS: P14.79, P14.80; also elsewhere on the board

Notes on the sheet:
Samtec Q Series Connectors QSS mates with QTS This cinnector accomidates stacking PCBs
Timer Signals
PACSAT BOARD IO
Needs a lot of work to define all IO and put the connections on proper pins.
EXTERNAL USB Interface

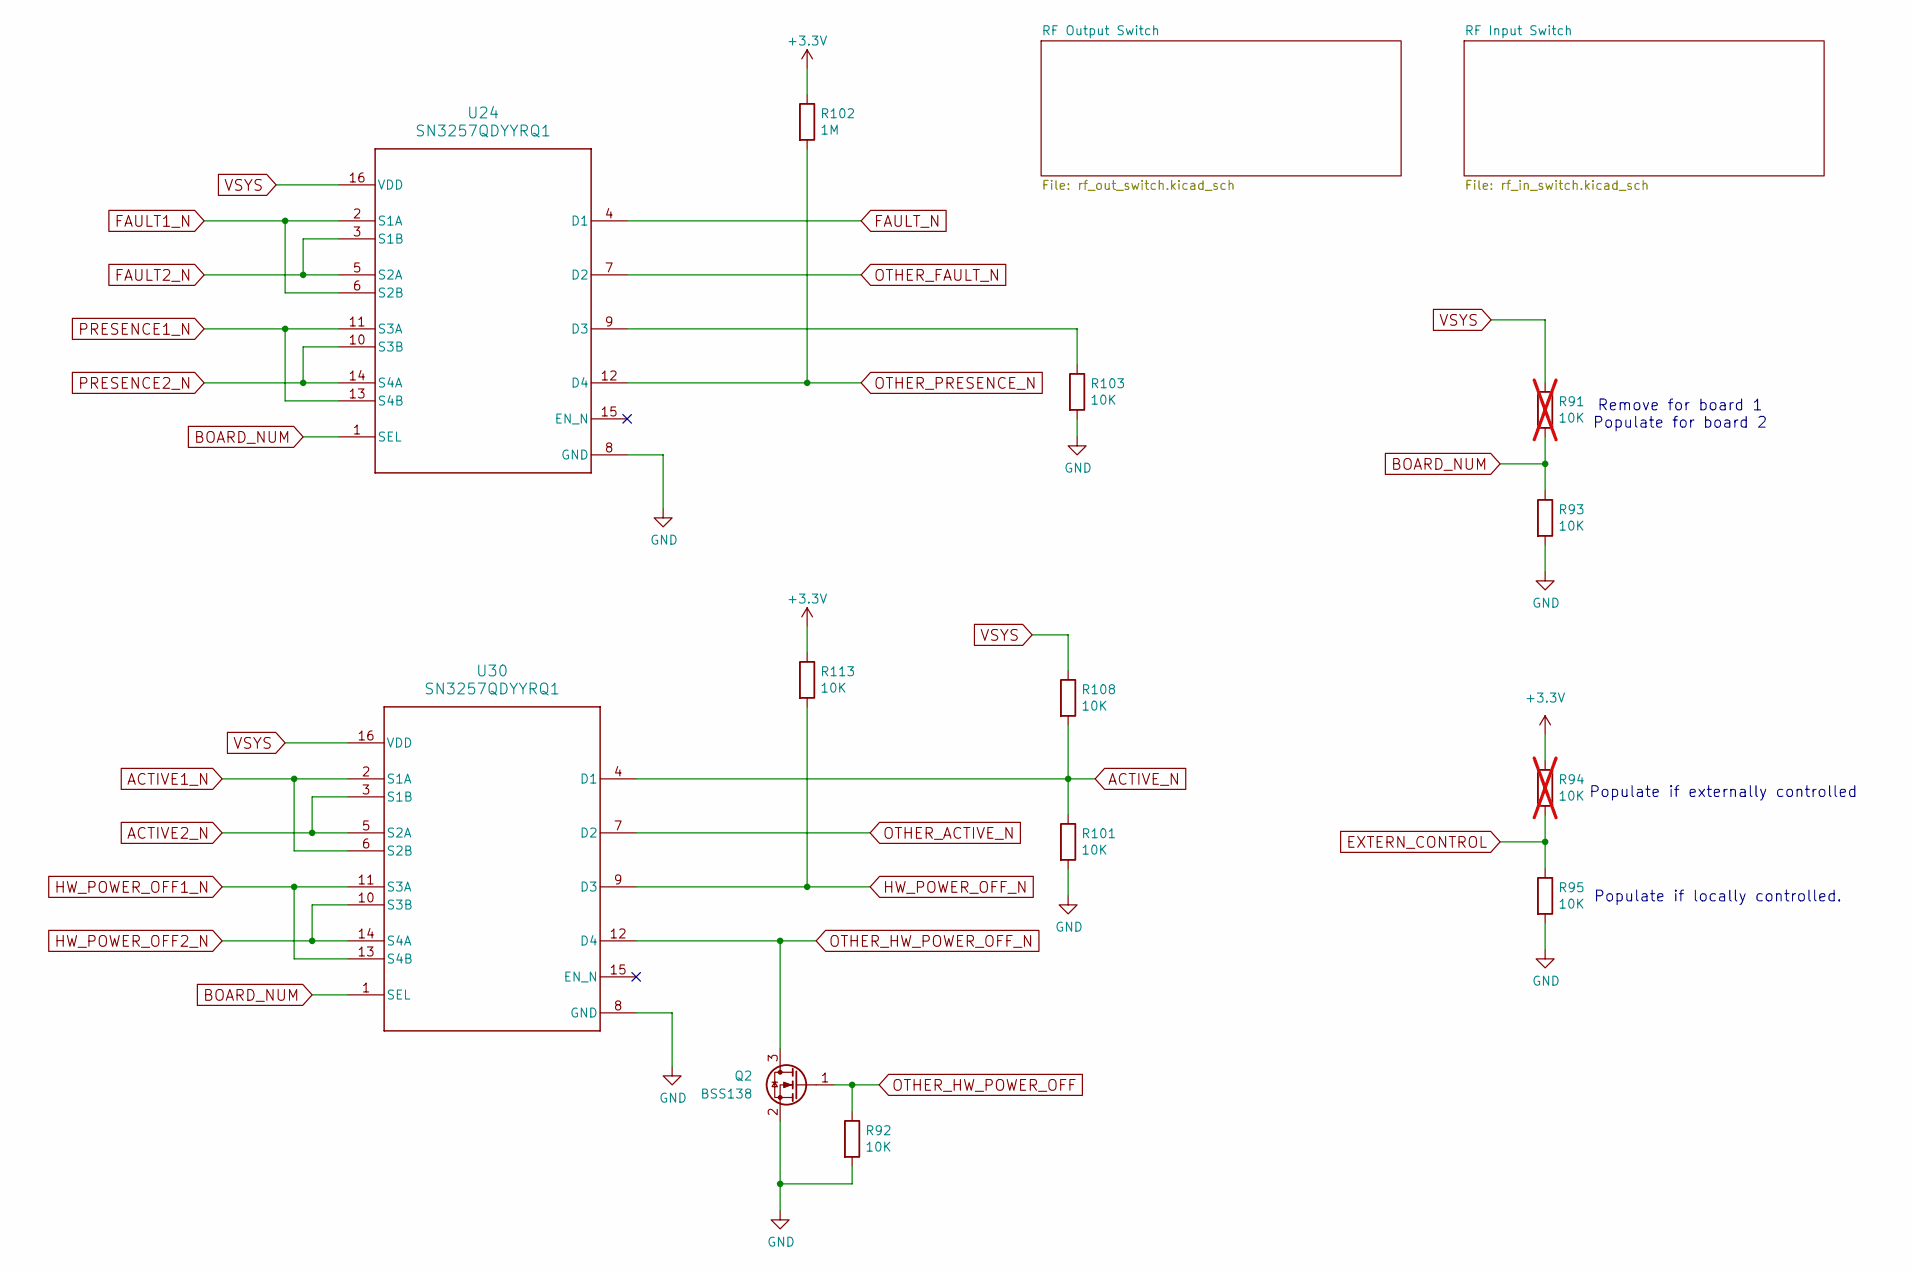
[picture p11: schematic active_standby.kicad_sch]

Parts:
Q2: BSS138; SOT-523
R91, R94: 10K; R_0402_1005Metric_Pad0.72x0.64mm_HandSolder; not fitted
R92, R93, R95, R101, R103, R108, R113: 10K; R_0402_1005Metric_Pad0.72x0.64mm_HandSolder
R102: 1M; R_0402_1005Metric_Pad0.72x0.64mm_HandSolder
U24, U30: SN3257QDYYRQ1; DYY0016A

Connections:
+3.3V: R94.1, R102.1, R113.1; also elsewhere on the board
ACTIVE1_N: U30.2 (S1A), U30.6 (S2B); also elsewhere on the board
ACTIVE2_N: U30.3 (S1B), U30.5 (S2A); also elsewhere on the board
ACTIVE_N: R101.1, R108.2, U30.4 (D1); also elsewhere on the board
BOARD_NUM: R91.2, R93.1, U24.1 (SEL), U30.1 (SEL); also elsewhere on the board
EXTERN_CONTROL: R94.2, R95.1; also elsewhere on the board
FAULT1_N: U24.2 (S1A), U24.6 (S2B); also elsewhere on the board
FAULT2_N: U24.3 (S1B), U24.5 (S2A); also elsewhere on the board
FAULT_N: U24.4 (D1); also elsewhere on the board
GND: Q2.2 (S), R92.2, R93.2, R95.2, R101.2, R103.2, U24.8 (GND), U30.8 (GND); also elsewhere on the board
HW_POWER_OFF1_N: U30.11 (S3A), U30.13 (S4B); also elsewhere on the board
HW_POWER_OFF2_N: U30.10 (S3B), U30.14 (S4A); also elsewhere on the board
HW_POWER_OFF_N: R113.2, U30.9 (D3); also elsewhere on the board
unnamed: R103.1, U24.9 (D3)
OTHER_ACTIVE_N: U30.7 (D2); also elsewhere on the board
OTHER_FAULT_N: U24.7 (D2); also elsewhere on the board
OTHER_HW_POWER_OFF: Q2.1 (G), R92.1; also elsewhere on the board
OTHER_HW_POWER_OFF_N: Q2.3 (D), U30.12 (D4); also elsewhere on the board
OTHER_PRESENCE_N: R102.2, U24.12 (D4); also elsewhere on the board
PRESENCE1_N: U24.11 (S3A), U24.13 (S4B); also elsewhere on the board
PRESENCE2_N: U24.10 (S3B), U24.14 (S4A); also elsewhere on the board
VSYS: R91.1, R108.1, U24.16 (VDD), U30.16 (VDD); also elsewhere on the board

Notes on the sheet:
Remove for board 1 Populate for board 2
Populate if externally controlled
Populate if locally controlled.

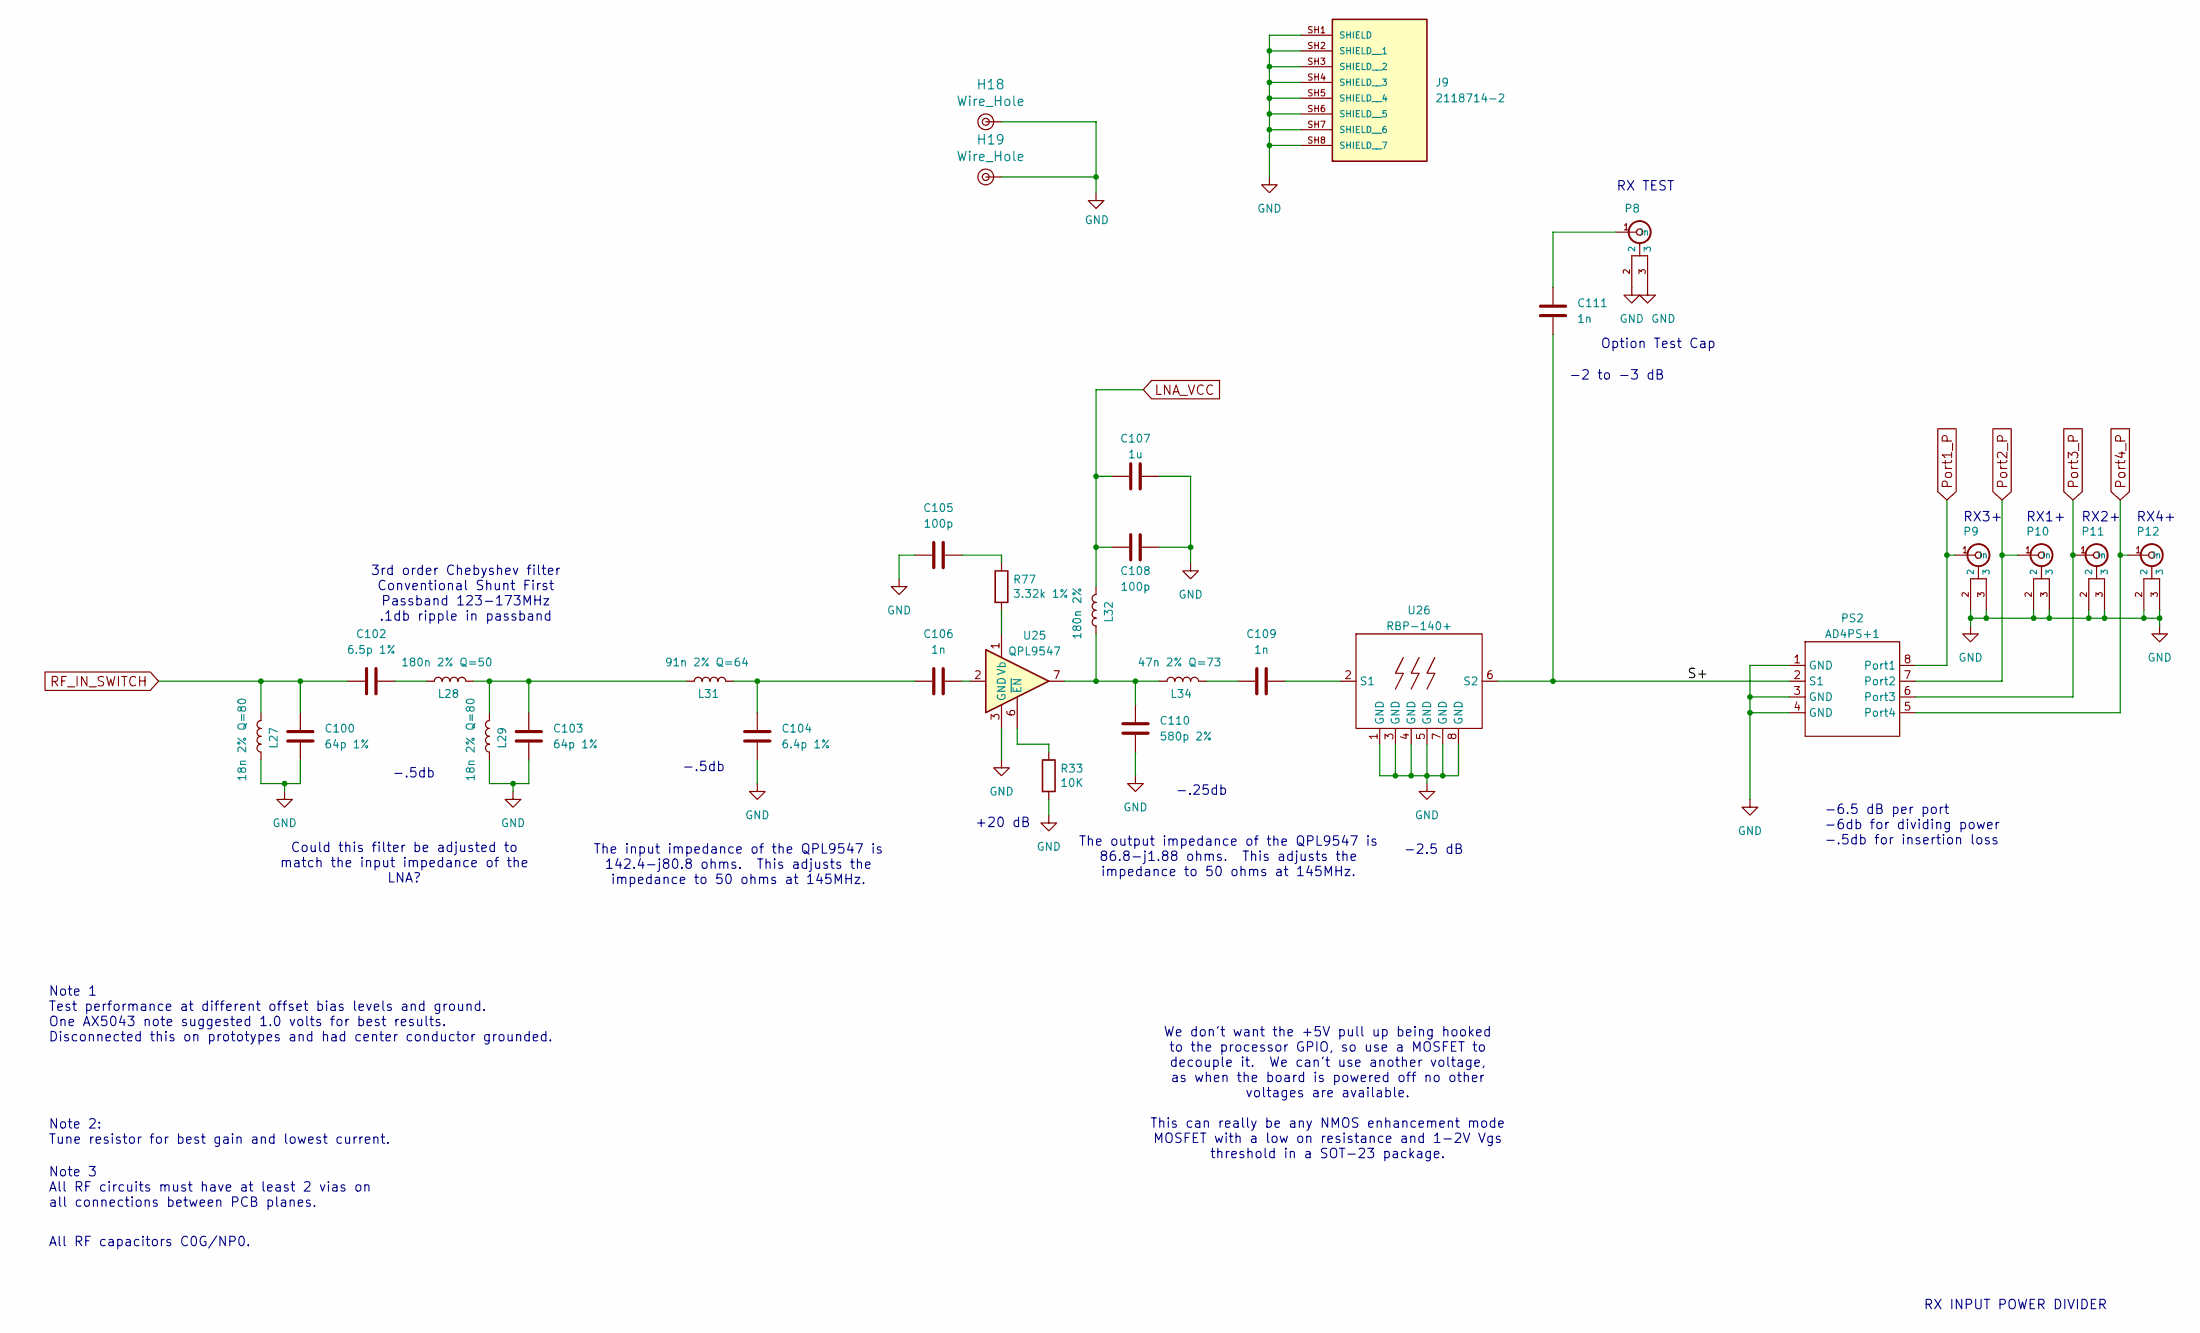
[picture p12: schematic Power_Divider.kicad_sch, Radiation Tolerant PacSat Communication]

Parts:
C100, C103: 64p 1%; C_0402_1005Metric_Pad0.74x0.62mm_HandSolder
C102: 6.5p 1%; C_0402_1005Metric_Pad0.74x0.62mm_HandSolder
C104: 6.4p 1%; C_0402_1005Metric_Pad0.74x0.62mm_HandSolder
C105, C108: 100p; C_0603_1608Metric_Pad1.08x0.95mm_HandSolder
C106, C109, C111: 1n; C_0402_1005Metric_Pad0.74x0.62mm_HandSolder
C107: 1u; C_0603_1608Metric_Pad1.08x0.95mm_HandSolder
C110: 580p 2%; C_0402_1005Metric_Pad0.74x0.62mm_HandSolder
H18, H19: Wire_Hole
J9: 2118714-2; TE_2118714-2; PARTREV A2
L27, L29: 18n 2% Q=80; L_0402_1005Metric_Pad0.77x0.64mm_HandSolder
L28: 180n 2% Q=50; L_0805_2012Metric
L31: 91n 2% Q=64; L_0603_1608Metric_Pad1.05x0.95mm_HandSolder
L32: 180n 2%; L_0603_1608Metric_Pad1.05x0.95mm_HandSolder
L34: 47n 2% Q=73; L_0603_1608Metric
P8: CONN1_CONUFL_TEC
P9, P10, P11, P12: CONUFL001-SMD-T; CONN1_CONUFL_TEC
PS2: AD4PS+1; CJ725
R33: 10K; R_0603_1608Metric_Pad0.98x0.95mm_HandSolder
R77: 3.32k 1%; R_0603_1608Metric_Pad0.98x0.95mm_HandSolder
U25: QPL9547; DFN-8-1EP_2x2mm_P0.5mm_EP0.8x1.6mm
U26: RBP-140+; Mini-Circuits_GP731

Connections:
/Rx_Power_Divider/S+: C111.2, PS2.2 (S1), U26.6 (S2)
GND: C100.1, C103.1, C104.2, C105.2, C107.1, C108.1, C110.1, H18.1, H19.1, J9.SH1 (SHIELD), J9.SH2 (SHIELD__1), J9.SH3 (SHIELD__2), J9.SH4 (SHIELD__3), J9.SH5 (SHIELD__4), J9.SH6 (SHIELD__5), J9.SH7 (SHIELD__6), J9.SH8 (SHIELD__7), L27.2, L29.2, P8.2, P8.3, P9.2, P9.3, P10.2, P10.3, P11.2, P11.3, P12.2, P12.3, PS2.1 (GND), PS2.3 (GND), PS2.4 (GND), R33.2, U25.3 (GND), U25.4 (GND), U25.5 (GND), U25.8 (GND), U25.9 (GND), U26.1 (GND), U26.3 (GND), U26.4 (GND), U26.5 (GND), U26.7 (GND), U26.8 (GND); also elsewhere on the board
LNA_VCC: C107.2, C108.2, L32.1; also elsewhere on the board
unnamed: C102.1, L28.2
unnamed: C103.2, L28.1, L29.1, L31.2
unnamed: C104.1, C106.2, L31.1
unnamed: C105.1, R77.1
unnamed: C106.1, U25.2
unnamed: C109.2, L34.1
unnamed: C110.2, L32.2, L34.2, U25.7
unnamed: C111.1, P8.1 (In)
unnamed: R77.2, U25.1 (Vb)
unnamed: R33.1, U25.6 (~EN)
unnamed: C109.1, U26.2 (S1)
Port1_P: P9.1 (In), PS2.8 (Port1); also elsewhere on the board
Port2_P: P10.1 (In), PS2.7 (Port2); also elsewhere on the board
Port3_P: P11.1 (In), PS2.6 (Port3); also elsewhere on the board
Port4_P: P12.1 (In), PS2.5 (Port4); also elsewhere on the board
RF_IN_SWITCH: C100.2, C102.2, L27.1; also elsewhere on the board

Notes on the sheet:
-6.5 dB per port -6db for dividing power -.5db for insertion loss
Note 1 Test performance at different offset bias levels and ground. One AX5043 note suggested 1.0 volts for best results. Disconnected this on prototypes and had center conductor grounded.
RX3+
3rd order Chebyshev filter Conventional Shunt First Passband 123-173MHz .1db ripple in passband
Note 3 All RF circuits must have at least 2 vias on all connections between PCB planes.
Note 2: Tune resistor for best gain and lowest current.
Option Test Cap
Could this filter be adjusted to match the input impedance of the LNA?
RX2+
RX1+
The output impedance of the QPL9547 is 86.8-j1.88 ohms. This adjusts the impedance to 50 ohms at 145MHz.
RX4+
-2.5 dB
RX INPUT POWER DIVIDER
-.25db
+20 dB
-.5db
-2 to -3 dB
The input impedance of the QPL9547 is 142.4-j80.8 ohms. This adjusts the impedance to 50 ohms at 145MHz.
We don't want the +5V pull up being hooked to the processor GPIO, so use a MOSFET to decouple it. We can't use another voltage, as when the board is powered off no other voltages are available. This can really be any NMOS enhancement mode MOSFET with a low on resistance and 1-2V Vgs threshold in a 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
RX TEST
All RF capacitors C0G/NP0.

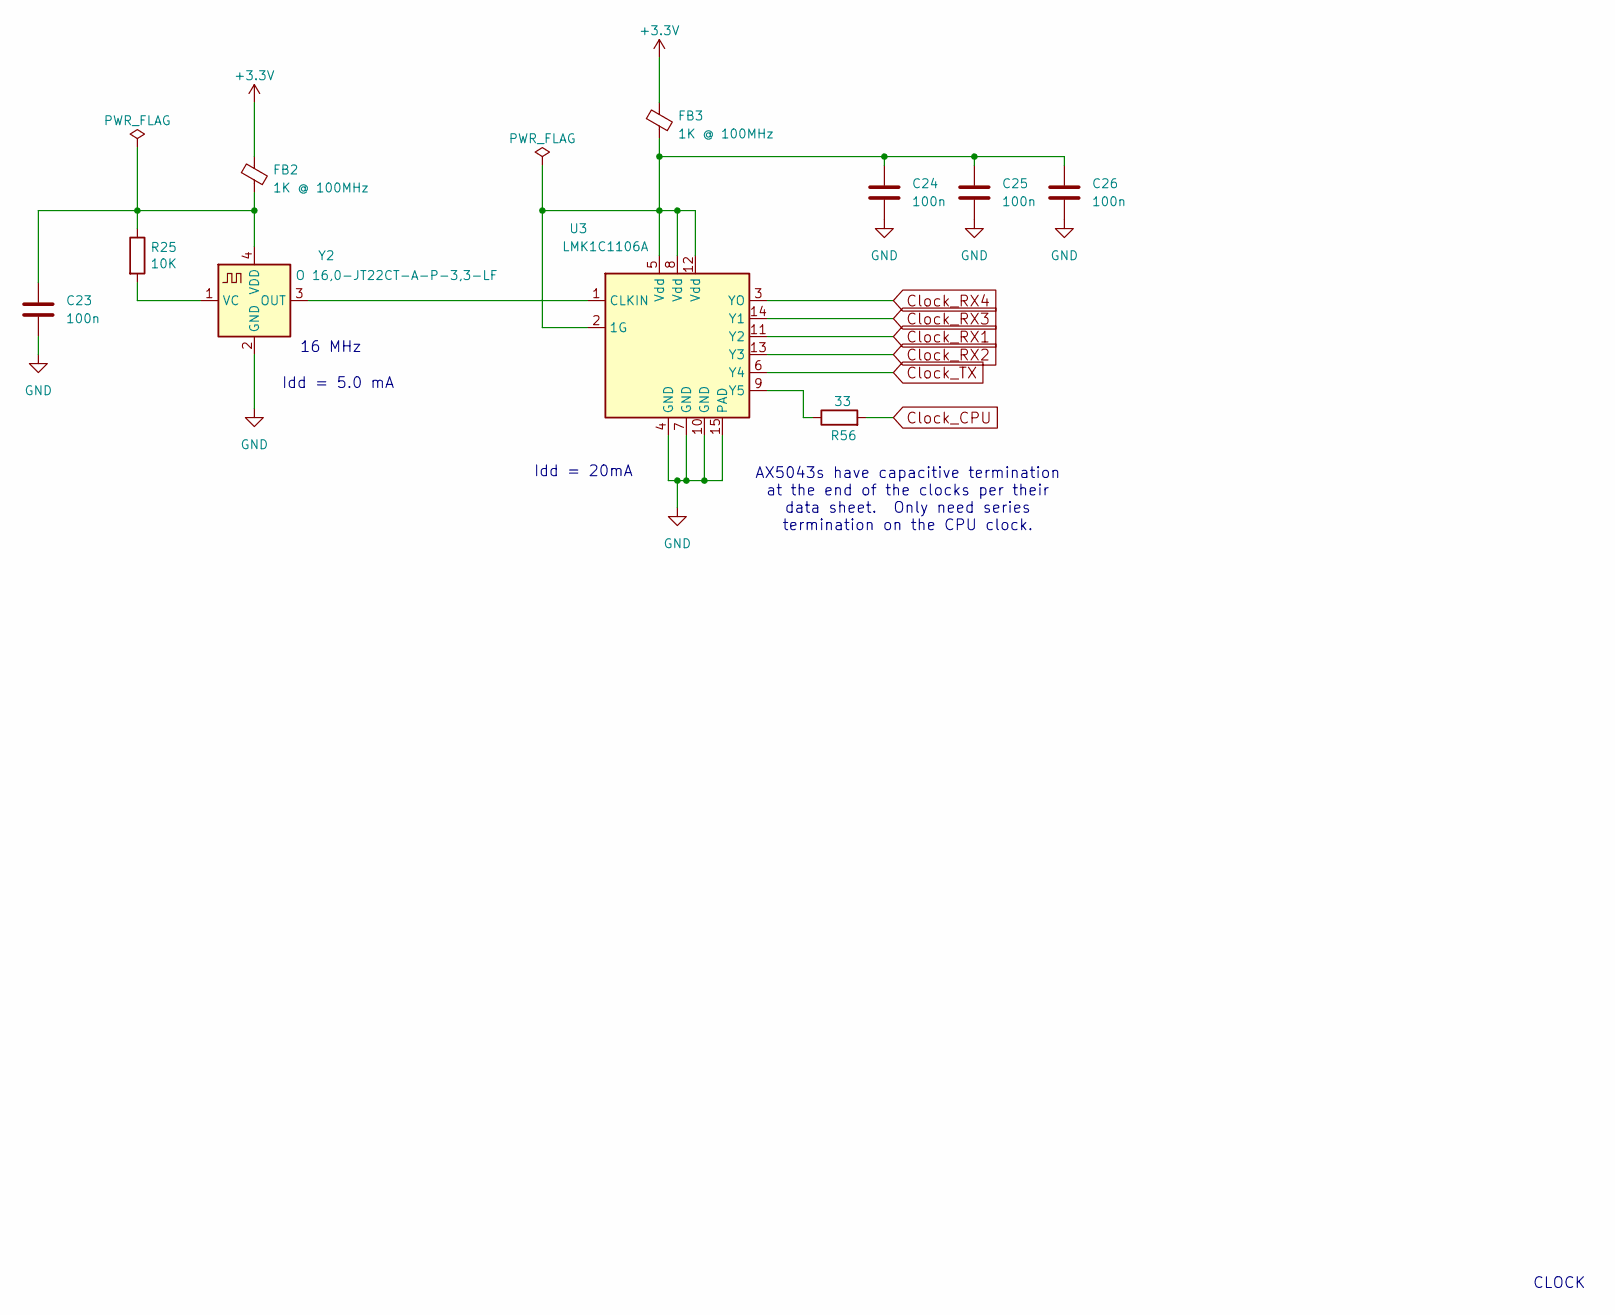
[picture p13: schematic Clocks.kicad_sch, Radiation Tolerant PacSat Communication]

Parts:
C23, C24, C25, C26: 100n; C_0402_1005Metric_Pad0.74x0.62mm_HandSolder
FB2, FB3: 1K @ 100MHz; R_0603_1608Metric_Pad0.98x0.95mm_HandSolder
R25: 10K; R_0402_1005Metric_Pad0.72x0.64mm_HandSolder
R56: 33; R_0402_1005Metric_Pad0.72x0.64mm_HandSolder
U3: LMK1C1106A; Texas_HTSSOP-14-1EP_4.4x5mm_P0.65mm_EP3.4x5mm_Mask3.155x3.2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
Y2: O 16,0-JT22CT-A-P-3,3-LF; Oscillator_SMD_SiT_PQFN-4Pin_2.5x2.0mm

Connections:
+3.3V: FB2.1, FB3.1; also elsewhere on the board
Clock_CPU: R56.2; also elsewhere on the board
Clock_RX1: U3.11 (Y2); also elsewhere on the board
Clock_RX2: U3.13 (Y3); also elsewhere on the board
Clock_RX3: U3.14 (Y1); also elsewhere on the board
Clock_RX4: U3.3 (YO); also elsewhere on the board
Clock_TX: U3.6 (Y4); also elsewhere on the board
GND: C23.2, C24.2, C25.2, C26.2, U3.4 (GND), U3.7 (GND), U3.10 (GND), U3.15 (PAD), Y2.2 (GND); also elsewhere on the board
unnamed: C24.1, C25.1, C26.1, FB3.2, U3.2 (1G), U3.5 (Vdd), U3.8 (Vdd), U3.12 (Vdd)
unnamed: U3.1 (CLKIN), Y2.3 (OUT)
unnamed: R56.1, U3.9 (Y5)
unnamed: R25.2, Y2.1 (VC)
unnamed: C23.1, FB2.2, R25.1, Y2.4 (VDD)

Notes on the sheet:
CLOCK
AX5043s have capacitive termination at the end of the clocks per their data sheet. Only need series termination on the CPU clock.
16 MHz
Idd = 20mA
Idd = 5.0 mA

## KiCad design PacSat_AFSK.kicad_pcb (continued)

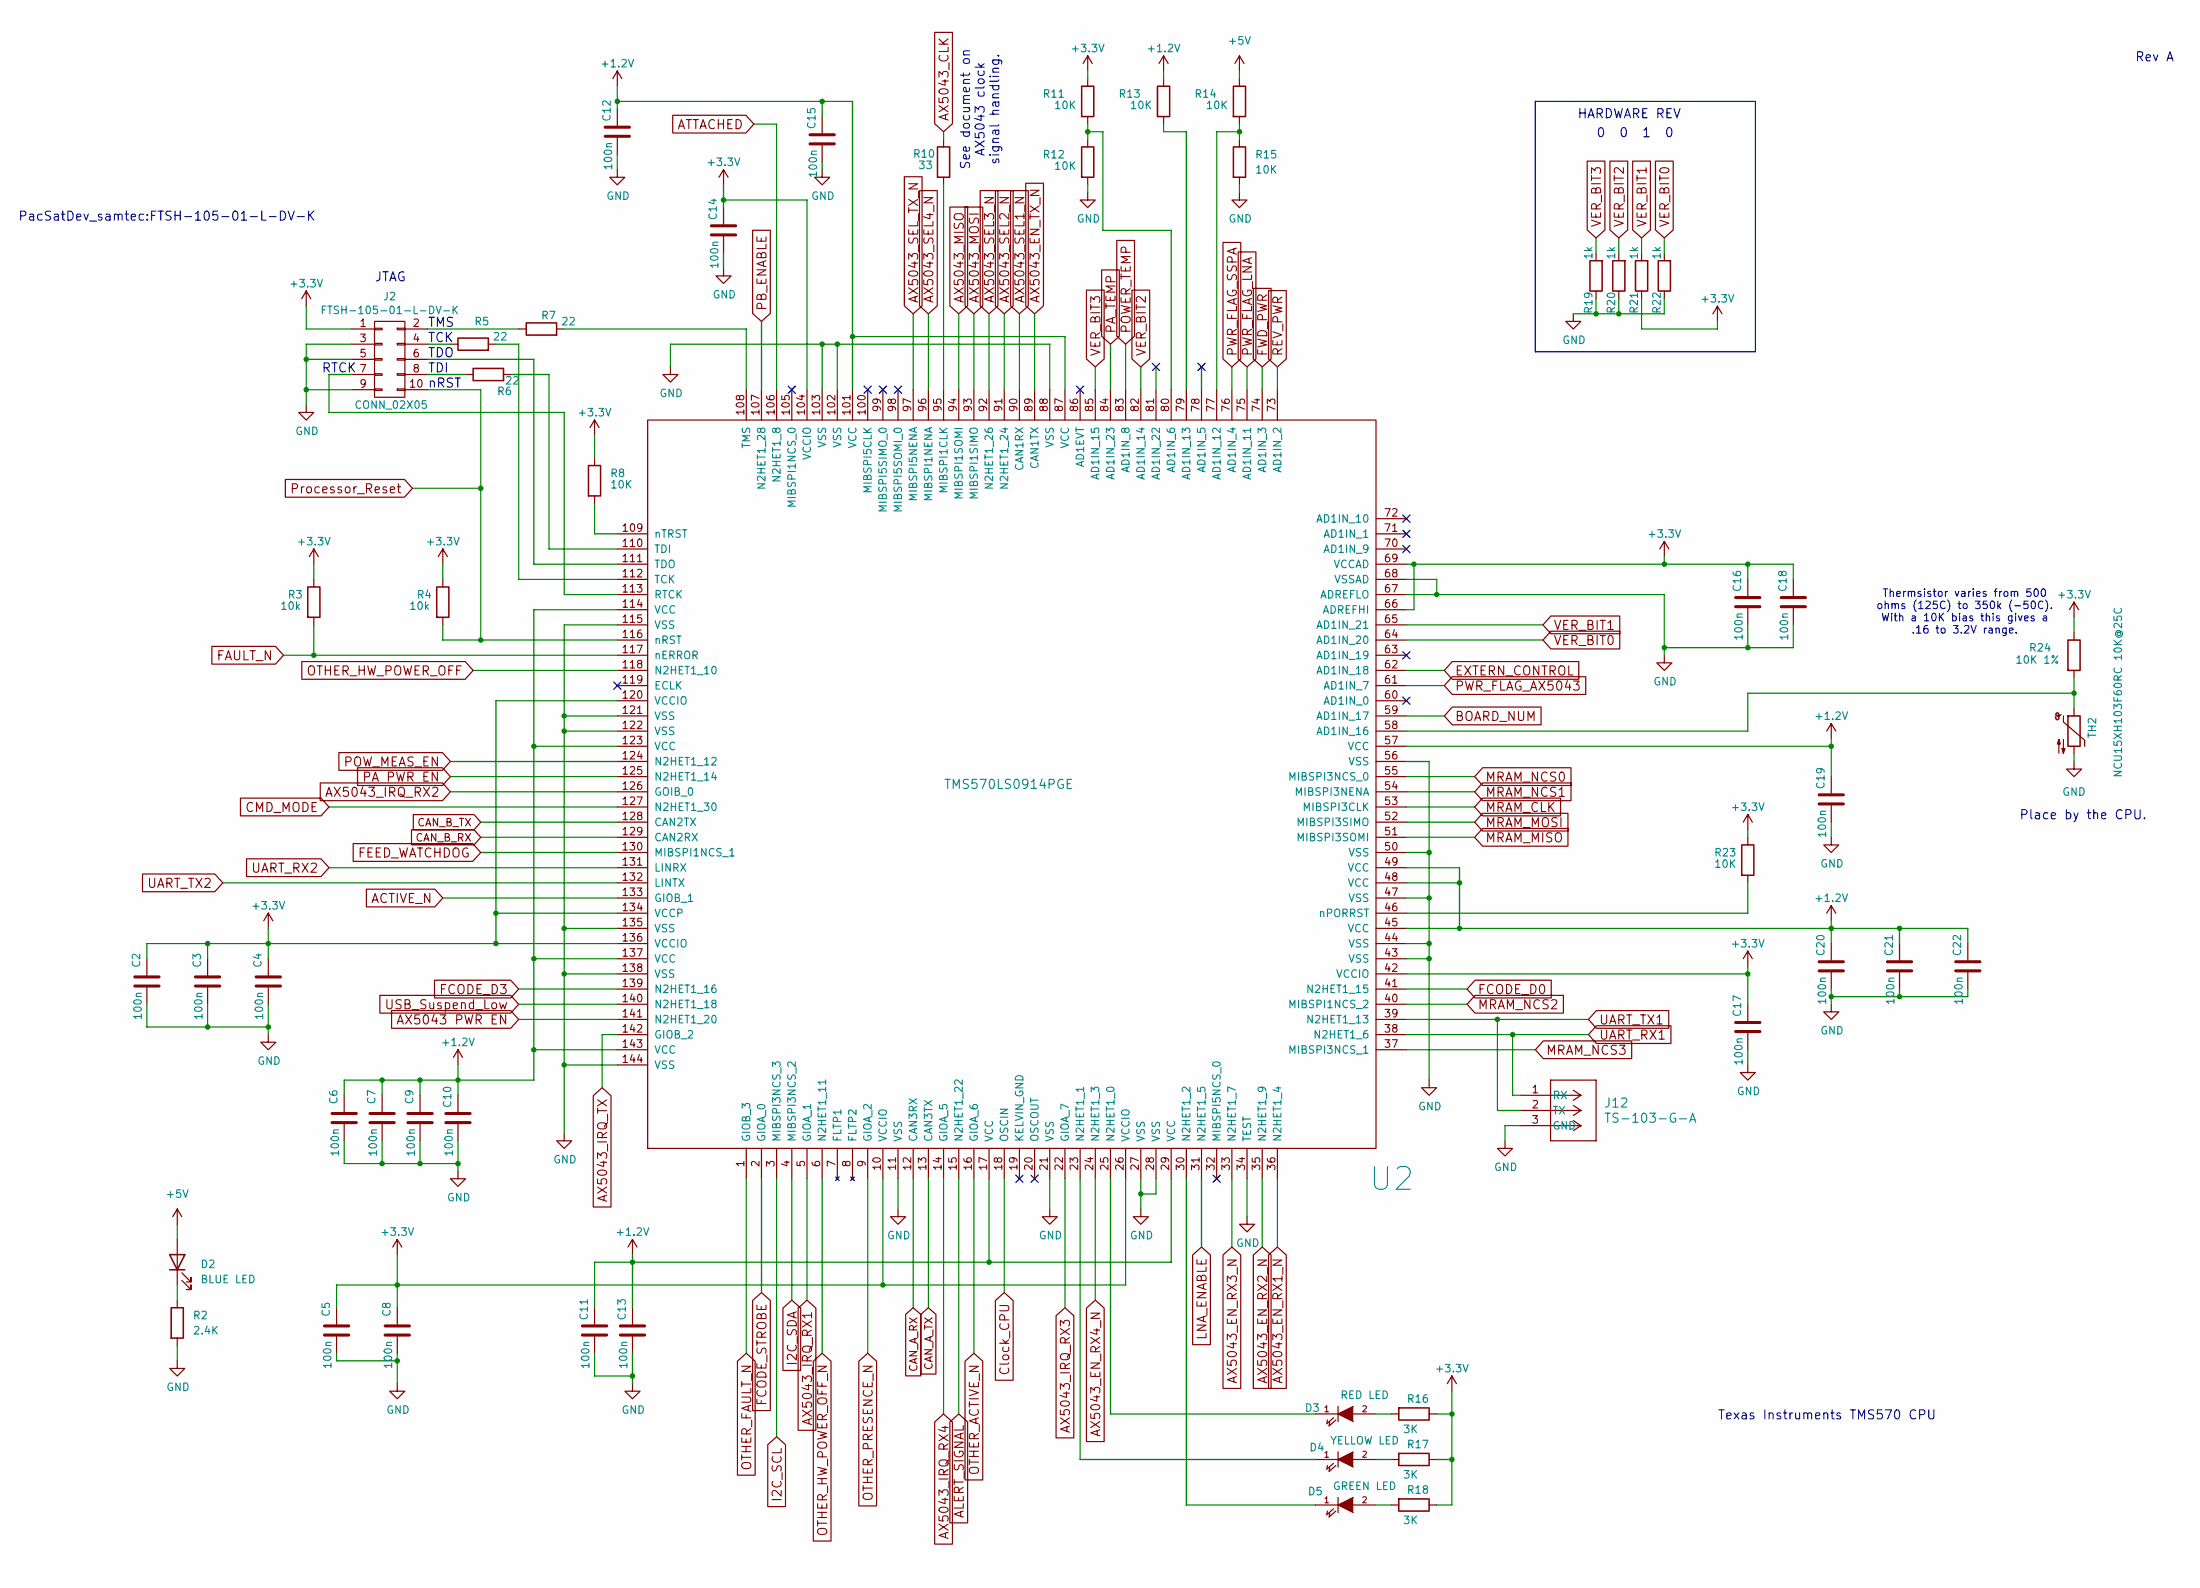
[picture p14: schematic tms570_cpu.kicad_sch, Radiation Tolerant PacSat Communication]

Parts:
C2, C3, C4, C5, C6, C7, C8, C9, C10, C11, C12, C13, C14, C15, C16, C17, C18, C19, C20, C21, C22: 100n; C_0402_1005Metric_Pad0.74x0.62mm_HandSolder
D2: BLUE LED; LED_0603_1608Metric_Pad1.05x0.95mm_HandSolder
D3: RED LED; LED_0603_1608Metric_Pad1.05x0.95mm_HandSolder
D4: YELLOW LED; LED_0603_1608Metric_Pad1.05x0.95mm_HandSolder
D5: GREEN LED; LED_0603_1608Metric_Pad1.05x0.95mm_HandSolder
J2: FTSH-105-01-L-DV-K
J12: TS-103-G-A; CON3_1X3_TU_HTS_SAI
R2: 2.4K; R_0603_1608Metric_Pad0.98x0.95mm_HandSolder
R3, R4: 10k; R_0402_1005Metric_Pad0.72x0.64mm_HandSolder
R5, R6, R7: 22; R_0402_1005Metric_Pad0.72x0.64mm_HandSolder
R8, R11, R12, R13, R14, R15, R23: 10K; R_0402_1005Metric_Pad0.72x0.64mm_HandSolder
R10: 33; R_0402_1005Metric_Pad0.72x0.64mm_HandSolder
R16, R17, R18: 3K; R_0603_1608Metric_Pad0.98x0.95mm_HandSolder
R19, R20, R21, R22: 1k; R_0402_1005Metric_Pad0.72x0.64mm_HandSolder
R24: 10K 1%; R_0402_1005Metric_Pad0.72x0.64mm_HandSolder
TH2: NCU15XH103F60RC 10K@25C; R_0402_1005Metric
U2: TMS570LS0914PGE; TQFP-144_20x20mm_Pitch0.5mm

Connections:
+1.2V: C6.1, C7.1, C9.1, C10.1, C11.1, C12.1, C13.1, C15.1, C19.1, C20.1, C21.1, C22.1, R13.1, U2.17 (VCC), U2.29 (VCC), U2.45 (VCC), U2.48 (VCC), U2.49 (VCC), U2.57 (VCC), U2.87 (VCC), U2.101 (VCC), U2.114 (VCC), U2.123 (VCC), U2.137 (VCC), U2.143 (VCC); also elsewhere on the board
+3.3V: C2.1, C3.1, C4.1, C5.1, C8.1, C14.1, C16.1, C17.1, C18.1, J2.1, R3.1, R4.1, R8.1, R11.1, R16.1, R17.1, R18.1, R21.1, R23.1, R24.1, U2.10 (VCCIO), U2.26 (VCCIO), U2.42 (VCCIO), U2.66 (ADREFHI), U2.69 (VCCAD), U2.104 (VCCIO), U2.120 (VCCIO), U2.134 (VCCP), U2.136 (VCCIO); also elsewhere on the board
+5V: D2.2 (A), R14.1; also elsewhere on the board
ACTIVE_N: U2.133 (GIOB_1); also elsewhere on the board
ALERT_SIGNAL: U2.15 (N2HET1_22); also elsewhere on the board
ATTACHED: U2.106 (N2HET1_8); also elsewhere on the board
AX5043 PWR EN: U2.141 (N2HET1_20); also elsewhere on the board
AX5043_CLK: R10.1; also elsewhere on the board
AX5043_EN_RX1_N: U2.36 (N2HET1_4); also elsewhere on the board
AX5043_EN_RX2_N: U2.35 (N2HET1_9); also elsewhere on the board
AX5043_EN_RX3_N: U2.33 (N2HET1_7); also elsewhere on the board
AX5043_EN_RX4_N: U2.24 (N2HET1_3); also elsewhere on the board
AX5043_EN_TX_N: U2.89 (CAN1TX); also elsewhere on the board
AX5043_IRQ_RX1: U2.5 (GIOA_1); also elsewhere on the board
AX5043_IRQ_RX2: U2.126 (GOIB_0); also elsewhere on the board
AX5043_IRQ_RX3: U2.22 (GIOA_7); also elsewhere on the board
AX5043_IRQ_RX4: U2.14 (GIOA_5); also elsewhere on the board
AX5043_IRQ_TX: U2.142 (GIOB_2); also elsewhere on the board
AX5043_MISO: U2.94 (MIBSPI1SOMI); also elsewhere on the board
AX5043_MOSI: U2.93 (MIBSPI1SIMO); also elsewhere on the board
AX5043_SEL1_N: U2.90 (CAN1RX); also elsewhere on the board
AX5043_SEL2_N: U2.91 (N2HET1_24); also elsewhere on the board
AX5043_SEL3_N: U2.92 (N2HET1_26); also elsewhere on the board
AX5043_SEL4_N: U2.96 (MIBSPI1NENA); also elsewhere on the board
AX5043_SEL_TX_N: U2.97 (MIBSPI5NENA); also elsewhere on the board
BOARD_NUM: U2.59 (AD1IN_17); also elsewhere on the board
CAN_A_RX: U2.12 (CAN3RX); also elsewhere on the board
CAN_A_TX: U2.13 (CAN3TX); also elsewhere on the board
CAN_B_RX: U2.129 (CAN2RX); also elsewhere on the board
CAN_B_TX: U2.128 (CAN2TX); also elsewhere on the board
CMD_MODE: U2.127 (N2HET1_30); also elsewhere on the board
Clock_CPU: U2.18 (OSCIN); also elsewhere on the board
EXTERN_CONTROL: U2.62 (AD1IN_18); also elsewhere on the board
FAULT_N: R3.2, U2.117 (nERROR); also elsewhere on the board
FCODE_D0: U2.41 (N2HET1_15); also elsewhere on the board
FCODE_D3: U2.139 (N2HET1_16); also elsewhere on the board
FCODE_STROBE: U2.2 (GIOA_0); also elsewhere on the board
FEED_WATCHDOG: U2.130 (MIBSPI1NCS_1); also elsewhere on the board
FWD_PWR: U2.74 (AD1IN_3); also elsewhere on the board
GND: C2.2, C3.2, C4.2, C5.2, C6.2, C7.2, C8.2, C9.2, C10.2, C11.2, C12.2, C13.2, C14.2, C15.2, C16.2, C17.2, C18.2, C19.2, C20.2, C21.2, C22.2, J2.3, J2.5, J2.9, J12.3 (GND), R2.2, R12.2, R15.2, R19.1, R20.1, R22.1, TH2.2, U2.11 (VSS), U2.21 (VSS), U2.27 (VSS), U2.28 (VSS), U2.34 (TEST), U2.43 (VSS), U2.44 (VSS), U2.47 (VSS), U2.50 (VSS), U2.56 (VSS), U2.67 (ADREFLO), U2.68 (VSSAD), U2.88 (VSS), U2.102 (VSS), U2.103 (VSS), U2.115 (VSS), U2.121 (VSS), U2.122 (VSS), U2.135 (VSS), U2.138 (VSS), U2.144 (VSS); also elsewhere on the board
I2C_SCL: U2.3 (MIBSPI3NCS_3); also elsewhere on the board
I2C_SDA: U2.4 (MIBSPI3NCS_2); also elsewhere on the board
LNA_ENABLE: U2.31 (N2HET1_5); also elsewhere on the board
MRAM_CLK: U2.53 (MIBSPI3CLK); also elsewhere on the board
MRAM_MISO: U2.51 (MIBSPI3SOMI); also elsewhere on the board
MRAM_MOSI: U2.52 (MIBSPI3SIMO); also elsewhere on the board
MRAM_NCS0: U2.55 (MIBSPI3NCS_0); also elsewhere on the board
MRAM_NCS1: U2.54 (MIBSPI3NENA); also elsewhere on the board
MRAM_NCS2: U2.40 (MIBSPI1NCS_2); also elsewhere on the board
MRAM_NCS3: U2.37 (MIBSPI3NCS_1); also elsewhere on the board
unnamed: D2.1 (K), R2.1
unnamed: D3.2 (A), R16.2
unnamed: D3.1 (K), U2.25 (N2HET1_0)
unnamed: D4.2 (A), R17.2
unnamed: D4.1 (K), U2.23 (N2HET1_1)
unnamed: D5.2 (A), R18.2
unnamed: D5.1 (K), U2.30 (N2HET1_2)
unnamed: J2.2, R7.1
unnamed: J2.4, R5.1
unnamed: J2.6, U2.111 (TDO)
unnamed: J2.7, U2.113 (RTCK)
unnamed: J2.8, R6.1
unnamed: R11.2, R12.1, U2.80 (AD1IN_6)
unnamed: R14.2, R15.1, U2.77 (AD1IN_12)
unnamed: R13.2, U2.79 (AD1IN_13)
unnamed: R24.2, TH2.1, U2.58 (AD1IN_16)
unnamed: R10.2, U2.95 (MIBSPI1CLK)
unnamed: R5.2, U2.112 (TCK)
unnamed: R6.2, U2.110 (TDI)
unnamed: R7.2, U2.108 (TMS)
unnamed: R23.2, U2.46 (nPORRST)
unnamed: R8.2, U2.109 (nTRST)
OTHER_ACTIVE_N: U2.16 (GIOA_6); also elsewhere on the board
OTHER_FAULT_N: U2.1 (GIOB_3); also elsewhere on the board
OTHER_HW_POWER_OFF: U2.118 (N2HET1_10); also elsewhere on the board
OTHER_HW_POWER_OFF_N: U2.6 (N2HET1_11); also elsewhere on the board
OTHER_PRESENCE_N: U2.9 (GIOA_2); also elsewhere on the board
PA PWR EN: U2.125 (N2HET1_14); also elsewhere on the board
PA_TEMP: U2.84 (AD1IN_23); also elsewhere on the board
PB_ENABLE: U2.107 (N2HET1_28); also elsewhere on the board
POWER_TEMP: U2.83 (AD1IN_8); also elsewhere on the board
POW_MEAS_EN: U2.124 (N2HET1_12); also elsewhere on the board
PWR_FLAG_AX5043: U2.61 (AD1IN_7); also elsewhere on the board
PWR_FLAG_LNA: U2.75 (AD1IN_11); also elsewhere on the board
PWR_FLAG_SSPA: U2.76 (AD1IN_4); also elsewhere on the board
Processor_Reset: J2.10, R4.2, U2.116 (nRST); also elsewhere on the board
REV_PWR: U2.73 (AD1IN_2); also elsewhere on the board
UART_RX1: J12.1 (RX), U2.38 (N2HET1_6); also elsewhere on the board
UART_RX2: U2.131 (LINRX); also elsewhere on the board
UART_TX1: J12.2 (TX), U2.39 (N2HET1_13); also elsewhere on the board
UART_TX2: U2.132 (LINTX); also elsewhere on the board
USB_Suspend_Low: U2.140 (N2HET1_18); also elsewhere on the board
VER_BIT0: R22.2, U2.64 (AD1IN_20)
VER_BIT1: R21.2, U2.65 (AD1IN_21)
VER_BIT2: R20.2, U2.82 (AD1IN_14)
VER_BIT3: R19.2, U2.85 (AD1IN_15)

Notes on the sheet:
Texas Instruments TMS570 CPU
RTCK
PacSatDev_samtec:FTSH-105-01-L-DV-K
See document on AX5043 clock signal handling.
TCK
Rev A
nRST
TDI
JTAG
Place by the CPU.
Thermsistor varies from 500 ohms (125C) to 350k (-50C). With a 10K bias this gives a .16 to 3.2V range.
HARDWARE REV
TDO
TMS

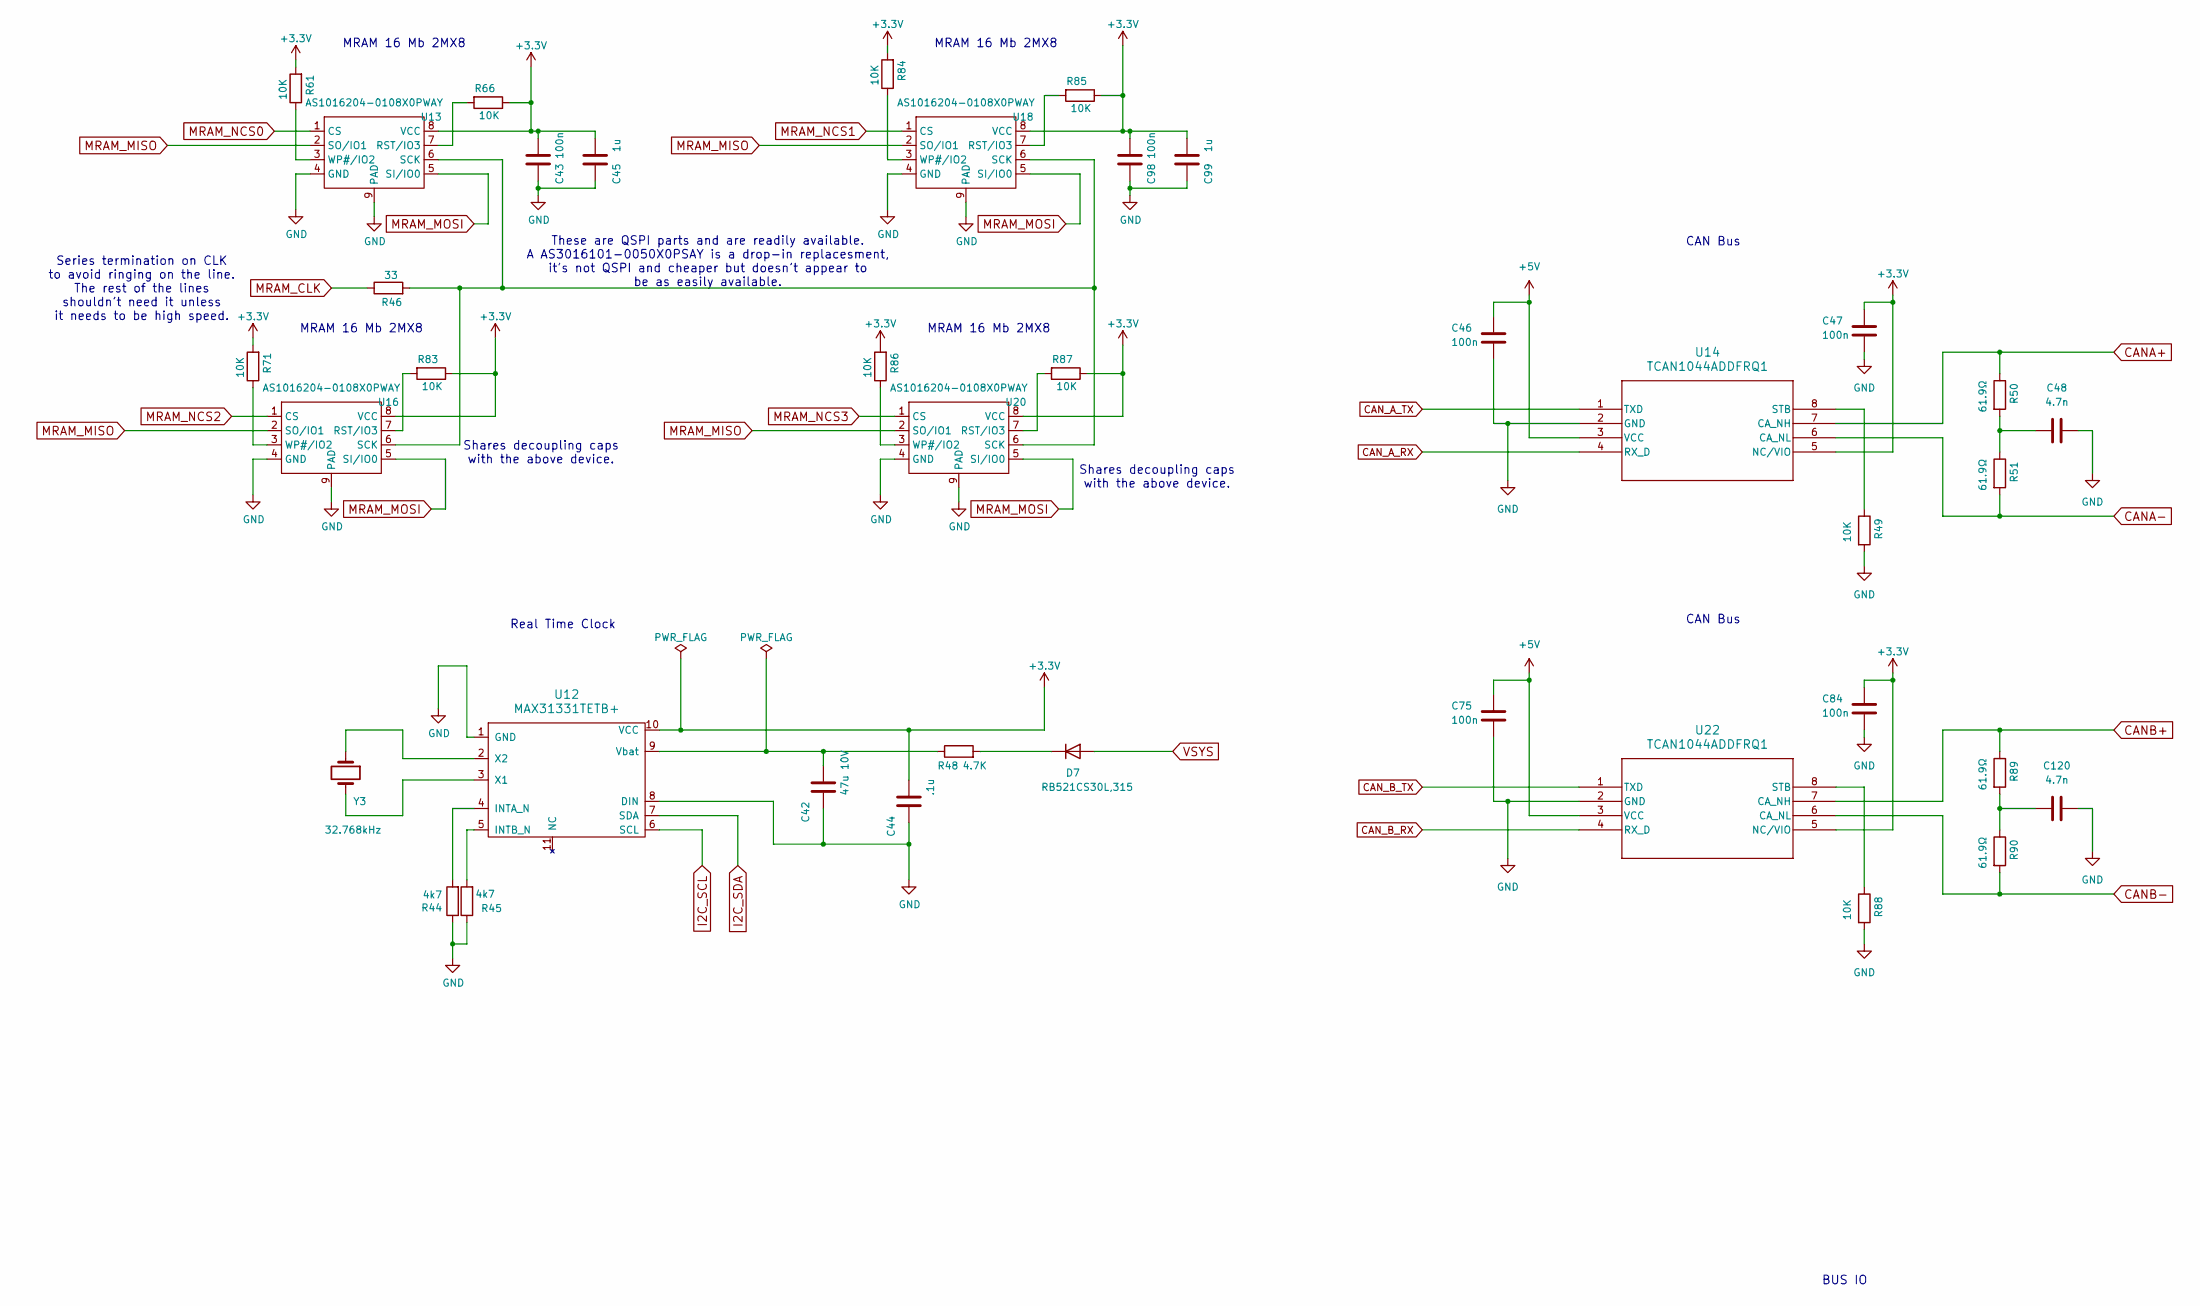
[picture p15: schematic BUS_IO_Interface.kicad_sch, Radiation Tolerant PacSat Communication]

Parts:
C42: 47u 10V; C_0805_2012Metric_Pad1.18x1.45mm_HandSolder
C43, C46, C47, C75, C84, C98: 100n; C_0402_1005Metric_Pad0.74x0.62mm_HandSolder
C44: .1u; C_0402_1005Metric_Pad0.74x0.62mm_HandSolder
C45, C99: 1u; C_0402_1005Metric_Pad0.74x0.62mm_HandSolder
C48, C120: 4.7n; C_0402_1005Metric_Pad0.74x0.62mm_HandSolder
D7: RB521CS30L,315; D_SOD-882
R44, R45: 4k7; R_0402_1005Metric_Pad0.72x0.64mm_HandSolder
R46: 33; R_0402_1005Metric_Pad0.72x0.64mm_HandSolder
R48: 4.7K; R_0402_1005Metric_Pad0.72x0.64mm_HandSolder
R49, R61, R66, R71, R83, R84, R85, R86, R87, R88: 10K; R_0402_1005Metric_Pad0.72x0.64mm_HandSolder
R50, R51, R89, R90: 61.9Ω; R_0402_1005Metric_Pad0.72x0.64mm_HandSolder
U12: MAX31331TETB+; TDFN-10-1EP_3x3mm_P0.5mm_EP0.9x2mm
U13, U16, U18, U20: AS1016204-0108X0PWAY; WSON-8-1EP_8x6mm_P1.27mm_EP3.4x4.3mm; PARTREV v3.2
U14, U22: TCAN1044ADDFRQ1; TSOT-23-8
Y3: 32.768kHz; Crystal_SMD_EuroQuartz_EQ161-2Pin_3.2x1.5mm

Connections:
+3.3V: C43.1, C44.1, C45.1, C47.1, C84.1, C98.1, C99.1, R61.2, R66.1, R71.2, R83.1, R84.2, R85.1, R86.2, R87.1, U12.10 (VCC), U13.8 (VCC), U14.5 (NC/VIO), U16.8 (VCC), U18.8 (VCC), U20.8 (VCC), U22.5 (NC/VIO); also elsewhere on the board
+5V: C46.1, C75.1, U14.3 (VCC), U22.3 (VCC); also elsewhere on the board
CANA+: R50.1, U14.7 (CA_NH); also elsewhere on the board
CANA-: R51.2, U14.6 (CA_NL); also elsewhere on the board
CANB+: R89.1, U22.7 (CA_NH); also elsewhere on the board
CANB-: R90.2, U22.6 (CA_NL); also elsewhere on the board
CAN_A_RX: U14.4 (RX_D); also elsewhere on the board
CAN_A_TX: U14.1 (TXD); also elsewhere on the board
CAN_B_RX: U22.4 (RX_D); also elsewhere on the board
CAN_B_TX: U22.1 (TXD); also elsewhere on the board
GND: C42.2, C43.2, C44.2, C45.2, C46.2, C47.2, C48.2, C75.2, C84.2, C98.2, C99.2, C120.2, R44.1, R45.1, R49.2, R88.2, U12.1 (GND), U12.8 (DIN), U13.4 (GND), U13.9 (PAD), U14.2 (GND), U16.4 (GND), U16.9 (PAD), U18.4 (GND), U18.9 (PAD), U20.4 (GND), U20.9 (PAD), U22.2 (GND); also elsewhere on the board
I2C_SCL: U12.6 (SCL); also elsewhere on the board
I2C_SDA: U12.7 (SDA); also elsewhere on the board
MRAM_CLK: R46.1; also elsewhere on the board
MRAM_MISO: U13.2 (SO/IO1), U16.2 (SO/IO1), U18.2 (SO/IO1), U20.2 (SO/IO1); also elsewhere on the board
MRAM_MOSI: U13.5 (SI/IO0), U16.5 (SI/IO0), U18.5 (SI/IO0), U20.5 (SI/IO0); also elsewhere on the board
MRAM_NCS0: U13.1 (CS); also elsewhere on the board
MRAM_NCS1: U18.1 (CS); also elsewhere on the board
MRAM_NCS2: U16.1 (CS); also elsewhere on the board
MRAM_NCS3: U20.1 (CS); also elsewhere on the board
unnamed: C48.1, R50.2, R51.1
unnamed: C120.1, R89.2, R90.1
unnamed: D7.1 (K), R48.2
unnamed: R44.2, U12.4 (INTA_N)
unnamed: R45.2, U12.5 (INTB_N)
unnamed: C42.1, R48.1, U12.9 (Vbat)
unnamed: U12.3 (X1), Y3.2
unnamed: U12.2 (X2), Y3.1
unnamed: R66.2, U13.7 (RST/IO3)
unnamed: R46.2, U13.6 (SCK), U16.6 (SCK), U18.6 (SCK), U20.6 (SCK)
unnamed: R61.1, U13.3 (WP#/IO2)
unnamed: R49.1, U14.8 (STB)
unnamed: R83.2, U16.7 (RST/IO3)
unnamed: R71.1, U16.3 (WP#/IO2)
unnamed: R85.2, U18.7 (RST/IO3)
unnamed: R84.1, U18.3 (WP#/IO2)
unnamed: R87.2, U20.7 (RST/IO3)
unnamed: R86.1, U20.3 (WP#/IO2)
unnamed: R88.1, U22.8 (STB)
VSYS: D7.2 (A); also elsewhere on the board

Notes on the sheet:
MRAM 16 Mb 2MX8
Series termination on CLK to avoid ringing on the line. The rest of the lines shouldn't need it unless it needs to be high speed.
These are QSPI parts and are readily available. A AS3016101-0050X0PSAY is a drop-in replacesment, it's not QSPI and cheaper but doesn't appear to be as easily available.
CAN Bus
Shares decoupling caps with the above device.
BUS IO
Real Time Clock

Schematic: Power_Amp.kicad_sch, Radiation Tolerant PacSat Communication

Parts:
C101, C116, C119: 1n; C_0402_1005Metric_Pad0.74x0.62mm_HandSolder
C112, C113, C115: 100p; C_0402_1005Metric_Pad0.74x0.62mm_HandSolder
C114: 39p 1%; C_0402_1005Metric_Pad0.74x0.62mm_HandSolder
C117: 130p 1% 30V; C_0603_1608Metric_Pad1.08x0.95mm_HandSolder
C118: 10u; C_0603_1608Metric_Pad1.08x0.95mm_HandSolder
FL2: LFCG-490+; GE0805C-2_MNC
H20, H21: Wire_Hole
J10: 2118718-2; TE_2118718-2; PARTREV A2
L35: 17n 2% Q>=40; L_0603_1608Metric_Pad1.05x0.95mm_HandSolder
L36: 68n; L_0603_1608Metric_Pad1.05x0.95mm_HandSolder
L37: 36n Q>40 I>1A; L_0603_1608Metric_Pad1.05x0.95mm_HandSolder
L38: 6.8n 2% Q=40; L_0603_1608Metric_Pad1.05x0.95mm_HandSolder
L39: 470n; L_0805_2012Metric_Pad1.15x1.40mm_HandSolder
P13: CONUFL001-SMD-T; CONN1_CONUFL_TEC
R78: 280; R_0402_1005Metric_Pad0.72x0.64mm_HandSolder
R79: 240; R_0402_1005Metric_Pad0.72x0.64mm_HandSolder
R80, R82: 49.9; R_0402_1005Metric_Pad0.72x0.64mm_HandSolder
R81: 10K 1%; R_0402_1005Metric_Pad0.72x0.64mm_HandSolder
TH4: NCU15XH103F60RC 10K@25C; R_0402_1005Metric
U27: TQP7M9106; QFN24_TQP7M9104_QOR
U28, U29: ADL5501AKSZ-R2; KS-6_ADI

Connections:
+3.3V: C101.2, C119.2, R81.1, U28.1 (VPOS), U29.1 (VPOS); also elsewhere on the board
FWD_PWR: U29.6 (VRMS); also elsewhere on the board
GND: C113.2, C114.2, C115.2, C116.2, C118.2, FL2.1 (GROUND), FL2.2 (GROUND), FL2.3 (GROUND), FL2.5 (GROUND), FL2.6 (GROUND), FL2.7 (GROUND), H20.1, H21.1, J10.SH1 (SHIELD), J10.SH2 (SHIELD__1), J10.SH3 (SHIELD__2), J10.SH4 (SHIELD__3), J10.SH5 (SHIELD__4), J10.SH6 (SHIELD__5), J10.SH7 (SHIELD__6), J10.SH8 (SHIELD__7), J10.SH9 (SHIELD__8), J10.SH10 (SHIELD__9), J10.SH11 (SHIELD__10), J10.SH12 (SHIELD__11), J10.SH13 (SHIELD__12), J10.SH14 (SHIELD__13), J10.SH15 (SHIELD__14), J10.SH16 (SHIELD__15), L38.2, L39.1, P13.2, P13.3, R80.2, R82.2, TH4.2, U27.2 (GND), U27.3 (GND), U27.6 (GND), U27.7 (GND), U27.8 (GND), U27.9 (GND), U27.10 (GND), U27.11 (GND), U27.12 (GND), U27.13 (GND), U27.17 (GND), U27.19 (GND), U27.20 (GND), U27.21 (GND), U27.22 (GND), U27.23 (GND), U27.24 (GND), U27.25 (RF/DC-GND), U28.4 (COMM), U29.4 (COMM); also elsewhere on the board
unnamed: C117.1, L37.1, U27.14 (RFOUT/VCC), U27.15 (RFOUT/VCC), U27.16 (RFOUT/VCC)
unnamed: C117.2, FL2.8 (INPUT), L38.1
unnamed: L35.2, U27.4 (RFIN), U27.5 (RFIN)
unnamed: L36.1, R79.1
unnamed: C112.2, C114.1, L35.1, P13.1 (In)
unnamed: R79.2, U27.18 (IREF)
unnamed: C113.1, R78.2, U27.1 (VBIAS)
unnamed: C119.1, U28.2 (FLTR)
unnamed: R80.1, R82.1, U28.3 (RFIN), U29.3 (RFIN)
unnamed: C101.1, U29.2 (FLTR)
PA_TEMP: R81.2, TH4.1; also elsewhere on the board
POW_MEAS_EN: U28.5 (ENBL), U29.5 (ENBL); also elsewhere on the board
REV_PWR: U28.6 (VRMS); also elsewhere on the board
RF_OUT_SWITCH: FL2.4 (OUTPUT), L39.2; also elsewhere on the board
SSPA_VCC: C115.1, C116.1, C118.1, L36.2, L37.2, R78.1; also elsewhere on the board
TX_OUT_DRV: C112.1; also elsewhere on the board

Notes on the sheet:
The cover for this frame is 2118717-4 and also needs to be ordered. When access to the parts is no longer needed (or shake resistance is required) the 2118708-4 has the same layout as a single unit.
Inductor to bleed of static build up on the antenna.
Place by the PA.
-1.3 dB
Thermsistor varies from 500 ohms (125C) to 350k (-50C). With a 10K bias this gives a .16 to 3.2V range.
33 dBm 2 W
RF POWER AMP
+20 dB
2W (33dBm) into 50 ohms is 10V RMS, ~14.3V peak to peak on the right side of the impedance converter. Pick appropriate devices.
TX_PA_DRV
DC bias may affect the value of this capacitor. May need to adjust.
Input impedance is 1.87 - 37.7j this matches to 50 ohms at 435MHz.
Output impedance is 6.23 - j13.3 ohms This converts to 50 ohms at 435MHz
Directional coupler 4mm long track width .1524mm with .127mm separation.

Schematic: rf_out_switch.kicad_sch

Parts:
P15, P16: CONUFL001-SMD-T; CONN1_CONUFL_TEC
R104, R109: 50R >=2W; R_1206_3216Metric_Pad1.30x1.75mm_HandSolder
R105, R106: 10K; R_0402_1005Metric_Pad0.72x0.64mm_HandSolder
R107: 0; R_0402_1005Metric_Pad0.72x0.64mm_HandSolder
U33, U34: QPC1022TR7; QPC1022_QOR

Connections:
+5V: R105.1, U33.7 (VDD), U34.7 (VDD); also elsewhere on the board
ACTIVE1_N: U33.5 (CTRL), U34.5 (CTRL); also elsewhere on the board
BOARD1_RF_BYPASS: R104.2; also elsewhere on the board
BOARD2_RF_BYPASS: R109.2; also elsewhere on the board
GND: P15.2, P15.3, P16.2, P16.3, R106.2, U33.1 (GND), U33.3 (GND), U33.9 (GND), U34.1 (GND), U34.3 (GND), U34.9 (GND); also elsewhere on the board
unnamed: P15.1 (In), R107.1, U33.2 (ANT), U34.4 (RF1)
unnamed: P16.1 (In), U34.2 (ANT)
unnamed: R104.1, U33.4 (RF1)
unnamed: R109.1, U34.8 (RF2)
RF_OUT_SWITCH: R107.2, U33.8 (RF2); also elsewhere on the board
RF_SWITCH_EN: R105.2, R106.1, U33.6 (EN), U34.6 (EN); also elsewhere on the board

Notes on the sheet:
TX ANT OUT
This RF switch setup handles active/standby on board 1. On board 1 the zero ohm resistor is not populated. On board 2 or on simplex boards none of the switch circuitry is populated and only the zero ohm resistor is populated.
TX FROM_BOARD2

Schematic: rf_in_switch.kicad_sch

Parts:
P17, P18: CONUFL001-SMD-T; CONN1_CONUFL_TEC
R96: 0; R_0402_1005Metric_Pad0.72x0.64mm_HandSolder
U31, U32: QPC1022TR7; QPC1022_QOR

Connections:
+5V: U31.7 (VDD), U32.7 (VDD); also elsewhere on the board
ACTIVE1_N: U31.5 (CTRL), U32.5 (CTRL); also elsewhere on the board
BOARD1_RF_BYPASS: U31.4 (RF1); also elsewhere on the board
BOARD2_RF_BYPASS: U32.8 (RF2); also elsewhere on the board
GND: P17.2, P17.3, P18.2, P18.3, U31.1 (GND), U31.3 (GND), U31.9 (GND), U32.1 (GND), U32.3 (GND), U32.9 (GND); also elsewhere on the board
unnamed: P17.1 (In), R96.1, U31.2 (ANT), U32.4 (RF1)
unnamed: P18.1 (In), U32.2 (ANT)
RF_IN_SWITCH: R96.2, U31.8 (RF2); also elsewhere on the board
RF_SWITCH_EN: U31.6 (EN), U32.6 (EN); also elsewhere on the board

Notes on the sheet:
RX FROM BOARD2
RX ANT IN
This RF switch setup handles active/standby on board 1. On board 1 the zero ohm resistor is not populated. On board 2 or on simplex boards none of the switch circuitry is populated and only the zero ohm resistor is populated.

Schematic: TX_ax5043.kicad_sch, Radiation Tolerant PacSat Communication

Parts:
C85, C86, C87: NS; C_0402_1005Metric_Pad0.74x0.62mm_HandSolder
C88: 5.1p 1%; C_0402_1005Metric_Pad0.74x0.62mm_HandSolder
C89: 11p 1%; C_0402_1005Metric_Pad0.74x0.62mm_HandSolder
C90: 5.6p 1%; C_0402_1005Metric_Pad0.74x0.62mm_HandSolder
C91, C92: 4.3p 1%; C_0402_1005Metric_Pad0.74x0.62mm_HandSolder
C93, C94, C97: 10n; C_0402_1005Metric_Pad0.74x0.62mm_HandSolder
C95: 6.8p; C_0402_1005Metric_Pad0.74x0.62mm_HandSolder
C96: 10p; C_0402_1005Metric_Pad0.74x0.62mm_HandSolder
FB8: 1K @ 100MHz; R_0603_1608Metric_Pad0.98x0.95mm_HandSolder
J7: 2118714-2; TE_2118714-2; PARTREV A2
L19, L26: 0; L_0603_1608Metric_Pad1.05x0.95mm_HandSolder
L20, L21: 27n 2% Q=40; L_0603_1608Metric_Pad1.05x0.95mm_HandSolder
L22, L23: 43n 2% Q=40; L_0603_1608Metric_Pad1.05x0.95mm_HandSolder
L24, L25: 100n; L_0603_1608Metric_Pad1.05x0.95mm_HandSolder
P6, P7: CONUFL001-SMD-T; CONN1_CONUFL_TEC
Q7: DMP2037U; SOT-23
R72: 50; R_0402_1005Metric_Pad0.72x0.64mm_HandSolder
R73, R74: 0R; R_0402_1005Metric_Pad0.72x0.64mm_HandSolder
R75: 470; R_0402_1005Metric_Pad0.72x0.64mm_HandSolder
U23: AX5043; QFN28

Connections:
/AX5043/TX_ax5043/TCANT_N: C92.1, L24.2, U23.4 (ANTN)
/AX5043/TX_ax5043/TXANT_P: C91.1, L25.2, U23.3 (ANTP)
/AX5043/TX_ax5043/TXa_N: C92.2, L23.2
/AX5043/TX_ax5043/TXa_P: C91.2, L22.2
/AX5043/TX_ax5043/TXb_N: C88.1, C90.1, L21.1, L23.1
/AX5043/TX_ax5043/TXb_P: C89.1, L20.2, L22.1
AX5043_3V3: Q7.2 (S); also elsewhere on the board
AX5043_CLK: R75.2; also elsewhere on the board
AX5043_EN_TX_N: Q7.1 (G); also elsewhere on the board
AX5043_IRQ_TX: U23.19 (IRQ); also elsewhere on the board
AX5043_MISO: U23.16 (MISO); also elsewhere on the board
AX5043_MOSI: U23.17 (MOSI); also elsewhere on the board
AX5043_SEL_TX_N: U23.14 (SEL); also elsewhere on the board
Clock_TX: C95.2, C96.1; also elsewhere on the board
GND: C85.2, C87.2, C89.2, C90.2, C93.2, C94.2, C95.1, C97.2, J7.SH1 (SHIELD), J7.SH2 (SHIELD__1), J7.SH3 (SHIELD__2), J7.SH4 (SHIELD__3), J7.SH5 (SHIELD__4), J7.SH6 (SHIELD__5), J7.SH7 (SHIELD__6), J7.SH8 (SHIELD__7), L21.2, L24.1, L25.1, P6.2, P6.3, P7.2, P7.3, R72.2, R73.2, R74.2, U23.0 (GND), U23.2 (GND), U23.6 (GND); also elsewhere on the board
unnamed: C86.1, C87.1, C88.2, L19.2, L20.1
unnamed: C93.1, U23.1 (VDD_ANA)
unnamed: C94.1, U23.7 (VDD_ANA)
unnamed: P7.1 (In), R72.1, U23.5 (ANTP1)
unnamed: FB8.2, Q7.3 (D)
unnamed: C96.2, U23.28 (CLK16P)
unnamed: R75.1, U23.15 (CLK)
unnamed: R73.1, U23.25 (GPADC1)
unnamed: R74.1, U23.26 (GPADC2)
unnamed: L26.2, U23.10 (L1)
unnamed: L26.1, U23.9 (L2)
unnamed: C97.1, FB8.1, U23.23 (VDD_IO)
TX_OUT_DRV: C85.1, C86.2, L19.1, P6.1 (In); also elsewhere on the board

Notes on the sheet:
TX_DRV
16 dBm Max Power Out @ 430 MHz If the PA works as expected, The maximum output here should be limited in the AX5043 to 13dBm to avoid overdriving the PA.
TRANSMITTER
While radio transceivers using power amplifiers with topologies such as class-A or class-B may have integrated amplifiers, AX5043 utilizes a class-E amplifier. Because of this, high efficiency power output can be achieved, though external components are required. AX5043 pins ANTP, ANTN, and ANTP1 a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
ALT TX Out
Shorting jumper if no inductor

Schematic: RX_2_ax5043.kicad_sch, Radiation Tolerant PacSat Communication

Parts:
C49: 100p; C_0402_1005Metric_Pad0.74x0.62mm_HandSolder
C50, C51: 15p; C_0402_1005Metric_Pad0.74x0.62mm_HandSolder
C52: 10n; C_0603_1608Metric_Pad1.08x0.95mm_HandSolder
C53, C56: 10n; C_0402_1005Metric_Pad0.74x0.62mm_HandSolder
C54: 6.8p; C_0402_1005Metric_Pad0.74x0.62mm_HandSolder
C55: 10p; C_0402_1005Metric_Pad0.74x0.62mm_HandSolder
FB5: 1K @ 100MHz; R_0603_1608Metric_Pad0.98x0.95mm_HandSolder
J3: 2118714-2; TE_2118714-2; PARTREV A2
L3, L4: 78n; L_0603_1608Metric_Pad1.05x0.95mm_HandSolder
L5: 1n; L_0603_1608Metric_Pad1.05x0.95mm_HandSolder
L6: 0; L_0603_1608Metric_Pad1.05x0.95mm_HandSolder
P2: CONUFL001-SMD-T; CONN1_CONUFL_TEC
Q4: DMP2037U; SOT-23
R52: 50; R_0402_1005Metric_Pad0.72x0.64mm_HandSolder
R55: 470; R_0402_1005Metric_Pad0.72x0.64mm_HandSolder
U15: AX5043; QFN28

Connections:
/AX5043/RX_2_ax5043/RX2ANT_N: C50.1, L4.2, U15.4 (ANTN)
/AX5043/RX_2_ax5043/RX2ANT_P: C51.2, L3.2, L5.2, U15.3 (ANTP)
AX5043_3V3: Q4.2 (S); also elsewhere on the board
AX5043_CLK: R55.2; also elsewhere on the board
AX5043_EN_RX2_N: Q4.1 (G); also elsewhere on the board
AX5043_IRQ_RX2: U15.19 (IRQ); also elsewhere on the board
AX5043_MISO: U15.16 (MISO); also elsewhere on the board
AX5043_MOSI: U15.17 (MOSI); also elsewhere on the board
AX5043_SEL2_N: U15.14 (SEL); also elsewhere on the board
Clock_RX2: C54.1, C55.1; also elsewhere on the board
GND: C51.1, C52.2, C53.2, C54.2, C56.2, J3.SH1 (SHIELD), J3.SH2 (SHIELD__1), J3.SH3 (SHIELD__2), J3.SH4 (SHIELD__3), J3.SH5 (SHIELD__4), J3.SH6 (SHIELD__5), J3.SH7 (SHIELD__6), J3.SH8 (SHIELD__7), L4.1, L5.1, P2.2, P2.3, R52.2, U15.0 (GND), U15.2 (GND), U15.6 (GND), U15.25 (GPADC1), U15.26 (GPADC2); also elsewhere on the board
unnamed: C52.1, U15.1 (VDD_ANA)
unnamed: C53.1, U15.7 (VDD_ANA)
unnamed: C49.2, C50.2, L3.1, P2.1 (In)
unnamed: FB5.2, Q4.3 (D)
unnamed: R52.1, U15.5 (ANTP1)
unnamed: C55.2, U15.28 (CLK16P)
unnamed: R55.1, U15.15 (CLK)
unnamed: L6.2, U15.10 (L1)
unnamed: L6.1, U15.9 (L2)
unnamed: C56.1, FB5.1, U15.23 (VDD_IO)
Port2_P: C49.1; also elsewhere on the board

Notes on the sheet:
See RX1 for Q values on inductors.
Rx2+
Shorting jumper if no inductor
RECEIVER 2

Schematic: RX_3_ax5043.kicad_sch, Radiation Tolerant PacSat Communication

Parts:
C58: 100p; C_0402_1005Metric_Pad0.74x0.62mm_HandSolder
C59, C60: 15p; C_0402_1005Metric_Pad0.74x0.62mm_HandSolder
C61, C62, C65: 10n; C_0402_1005Metric_Pad0.74x0.62mm_HandSolder
C63: 6.8p; C_0402_1005Metric_Pad0.74x0.62mm_HandSolder
C64: 10p; C_0402_1005Metric_Pad0.74x0.62mm_HandSolder
FB6: 1K @ 100MHz; R_0603_1608Metric_Pad0.98x0.95mm_HandSolder
J4: 2118714-2; TE_2118714-2; PARTREV A2
L7, L8: 78n; L_0603_1608Metric_Pad1.05x0.95mm_HandSolder
L9: 1n; L_0603_1608Metric_Pad1.05x0.95mm_HandSolder
L10: 0; L_0603_1608Metric_Pad1.05x0.95mm_HandSolder
P3: CONUFL001-SMD-T; CONN1_CONUFL_TEC
Q5: DMP2037U; SOT-23
R57: 50; R_0402_1005Metric_Pad0.72x0.64mm_HandSolder
R60: 470; R_0402_1005Metric_Pad0.72x0.64mm_HandSolder
U17: AX5043; QFN28

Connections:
/AX5043/RX_3_ax5043/RX3_N: C59.1, L8.2, U17.4 (ANTN)
/AX5043/RX_3_ax5043/RX3_P: C60.2, L7.2, L9.2, U17.3 (ANTP)
AX5043_3V3: Q5.2 (S); also elsewhere on the board
AX5043_CLK: R60.2; also elsewhere on the board
AX5043_EN_RX3_N: Q5.1 (G); also elsewhere on the board
AX5043_IRQ_RX3: U17.19 (IRQ); also elsewhere on the board
AX5043_MISO: U17.16 (MISO); also elsewhere on the board
AX5043_MOSI: U17.17 (MOSI); also elsewhere on the board
AX5043_SEL3_N: U17.14 (SEL); also elsewhere on the board
Clock_RX3: C63.1, C64.1; also elsewhere on the board
GND: C60.1, C61.2, C62.2, C63.2, C65.2, J4.SH1 (SHIELD), J4.SH2 (SHIELD__1), J4.SH3 (SHIELD__2), J4.SH4 (SHIELD__3), J4.SH5 (SHIELD__4), J4.SH6 (SHIELD__5), J4.SH7 (SHIELD__6), J4.SH8 (SHIELD__7), L8.1, L9.1, P3.2, P3.3, R57.2, U17.0 (GND), U17.2 (GND), U17.6 (GND), U17.25 (GPADC1), U17.26 (GPADC2); also elsewhere on the board
unnamed: C61.1, U17.1 (VDD_ANA)
unnamed: C62.1, U17.7 (VDD_ANA)
unnamed: C58.2, C59.2, L7.1, P3.1 (In)
unnamed: FB6.2, Q5.3 (D)
unnamed: R57.1, U17.5 (ANTP1)
unnamed: C64.2, U17.28 (CLK16P)
unnamed: R60.1, U17.15 (CLK)
unnamed: L10.2, U17.10 (L1)
unnamed: L10.1, U17.9 (L2)
unnamed: C65.1, FB6.1, U17.23 (VDD_IO)
Port3_P: C58.1; also elsewhere on the board

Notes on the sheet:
RECEIVER 3
Shorting jumper if no inductor
See RX1 for Q values on inductors.
RX3+

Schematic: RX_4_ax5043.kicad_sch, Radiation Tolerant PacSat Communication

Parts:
C67: 100p; C_0402_1005Metric_Pad0.74x0.62mm_HandSolder
C68, C69: 15p; C_0402_1005Metric_Pad0.74x0.62mm_HandSolder
C70, C71, C74: 10n; C_0402_1005Metric_Pad0.74x0.62mm_HandSolder
C72: 6.8p; C_0402_1005Metric_Pad0.74x0.62mm_HandSolder
C73: 10p; C_0402_1005Metric_Pad0.74x0.62mm_HandSolder
FB7: 1K @ 100MHz; R_0603_1608Metric_Pad0.98x0.95mm_HandSolder
J5: 2118714-2; TE_2118714-2; PARTREV A2
L11, L12: 78n; L_0603_1608Metric_Pad1.05x0.95mm_HandSolder
L13: 1n; L_0603_1608Metric_Pad1.05x0.95mm_HandSolder
L14: 0; L_0603_1608Metric_Pad1.05x0.95mm_HandSolder
P4: CONUFL001-SMD-T; CONN1_CONUFL_TEC
Q6: DMP2037U; SOT-23
R62: 50; R_0402_1005Metric_Pad0.72x0.64mm_HandSolder
R65: 470; R_0402_1005Metric_Pad0.72x0.64mm_HandSolder
U19: AX5043; QFN28

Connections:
/AX5043/RX_4_ax5043/RX4ANT_N: C68.1, L12.2, U19.4 (ANTN)
/AX5043/RX_4_ax5043/RX4ANT_P: C69.2, L11.2, L13.2, U19.3 (ANTP)
AX5043_3V3: Q6.2 (S); also elsewhere on the board
AX5043_CLK: R65.2; also elsewhere on the board
AX5043_EN_RX4_N: Q6.1 (G); also elsewhere on the board
AX5043_IRQ_RX4: U19.19 (IRQ); also elsewhere on the board
AX5043_MISO: U19.16 (MISO); also elsewhere on the board
AX5043_MOSI: U19.17 (MOSI); also elsewhere on the board
AX5043_SEL4_N: U19.14 (SEL); also elsewhere on the board
Clock_RX4: C72.1, C73.1; also elsewhere on the board
GND: C69.1, C70.2, C71.2, C72.2, C74.2, J5.SH1 (SHIELD), J5.SH2 (SHIELD__1), J5.SH3 (SHIELD__2), J5.SH4 (SHIELD__3), J5.SH5 (SHIELD__4), J5.SH6 (SHIELD__5), J5.SH7 (SHIELD__6), J5.SH8 (SHIELD__7), L12.1, L13.1, P4.2, P4.3, R62.2, U19.0 (GND), U19.2 (GND), U19.6 (GND), U19.25 (GPADC1), U19.26 (GPADC2); also elsewhere on the board
unnamed: C70.1, U19.1 (VDD_ANA)
unnamed: C71.1, U19.7 (VDD_ANA)
unnamed: C67.2, C68.2, L11.1, P4.1 (In)
unnamed: FB7.2, Q6.3 (D)
unnamed: R62.1, U19.5 (ANTP1)
unnamed: C73.2, U19.28 (CLK16P)
unnamed: R65.1, U19.15 (CLK)
unnamed: L14.2, U19.10 (L1)
unnamed: L14.1, U19.9 (L2)
unnamed: C74.1, FB7.1, U19.23 (VDD_IO)
Port4_P: C67.1; also elsewhere on the board

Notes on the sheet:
RECEIVER 4
Shorting jumper if no inductor
Rx4+
See RX1 for Q values on inductors.

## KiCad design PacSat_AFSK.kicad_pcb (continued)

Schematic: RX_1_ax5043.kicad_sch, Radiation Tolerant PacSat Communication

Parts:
C76: 100p; C_0402_1005Metric_Pad0.74x0.62mm_HandSolder
C77, C78: 15p; C_0402_1005Metric_Pad0.74x0.62mm_HandSolder
C79: 10n; C_0603_1608Metric_Pad1.08x0.95mm_HandSolder
C80, C83: 10n; C_0402_1005Metric_Pad0.74x0.62mm_HandSolder
C81: 6.8p; C_0402_1005Metric_Pad0.74x0.62mm_HandSolder
C82: 10p; C_0402_1005Metric_Pad0.74x0.62mm_HandSolder
FB4: 1K @ 100MHz; R_0603_1608Metric_Pad0.98x0.95mm_HandSolder
J6: 2118714-2; TE_2118714-2; PARTREV A2
L15, L16: 78n 2% Q=28; L_0603_1608Metric_Pad1.05x0.95mm_HandSolder
L17: 1n Q=12; L_0603_1608Metric_Pad1.05x0.95mm_HandSolder
L18: 0; L_0603_1608Metric_Pad1.05x0.95mm_HandSolder
P5: CONUFL001-SMD-T; CONN1_CONUFL_TEC
Q3: DMP2037U; SOT-23
R67: 50; R_0402_1005Metric_Pad0.72x0.64mm_HandSolder
R70: 470; R_0402_1005Metric_Pad0.72x0.64mm_HandSolder
U21: AX5043; QFN28

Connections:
/AX5043/RX_1_ax5043/RXANT_N: C77.1, L16.2, U21.4 (ANTN)
/AX5043/RX_1_ax5043/RXANT_P: C78.2, L15.2, L17.2, U21.3 (ANTP)
AX5043_3V3: Q3.2 (S); also elsewhere on the board
AX5043_CLK: R70.2; also elsewhere on the board
AX5043_EN_RX1_N: Q3.1 (G); also elsewhere on the board
AX5043_IRQ_RX1: U21.19 (IRQ); also elsewhere on the board
AX5043_MISO: U21.16 (MISO); also elsewhere on the board
AX5043_MOSI: U21.17 (MOSI); also elsewhere on the board
AX5043_SEL1_N: U21.14 (SEL); also elsewhere on the board
Clock_RX1: C81.1, C82.1; also elsewhere on the board
GND: C78.1, C79.2, C80.1, C81.2, C83.2, J6.SH1 (SHIELD), J6.SH2 (SHIELD__1), J6.SH3 (SHIELD__2), J6.SH4 (SHIELD__3), J6.SH5 (SHIELD__4), J6.SH6 (SHIELD__5), J6.SH7 (SHIELD__6), J6.SH8 (SHIELD__7), L16.1, L17.1, P5.2, P5.3, R67.2, U21.0 (GND), U21.2 (GND), U21.6 (GND), U21.25 (GPADC1), U21.26 (GPADC2); also elsewhere on the board
unnamed: C79.1, U21.1 (VDD_ANA)
unnamed: C80.2, U21.7 (VDD_ANA)
unnamed: C76.2, C77.2, L15.1, P5.1 (In)
unnamed: FB4.2, Q3.3 (D)
unnamed: R67.1, U21.5 (ANTP1)
unnamed: C82.2, U21.28 (CLK16P)
unnamed: R70.1, U21.15 (CLK)
unnamed: L18.2, U21.10 (L1)
unnamed: L18.1, U21.9 (L2)
unnamed: C83.1, FB4.1, U21.23 (VDD_IO)
Port1_P: C76.1; also elsewhere on the board

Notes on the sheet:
RECEIVER 1
The cover for this frame is 2118713-4 and also needs to be ordered. When access to the parts is no longer needed (or shake resistance is required) the 2118706-4 has the same layout as a single unit. This is the same for all shields on the AX5043 parts.
All RF capacitors C0G/NP0.
RX1+
Shorting jumper if no inductor

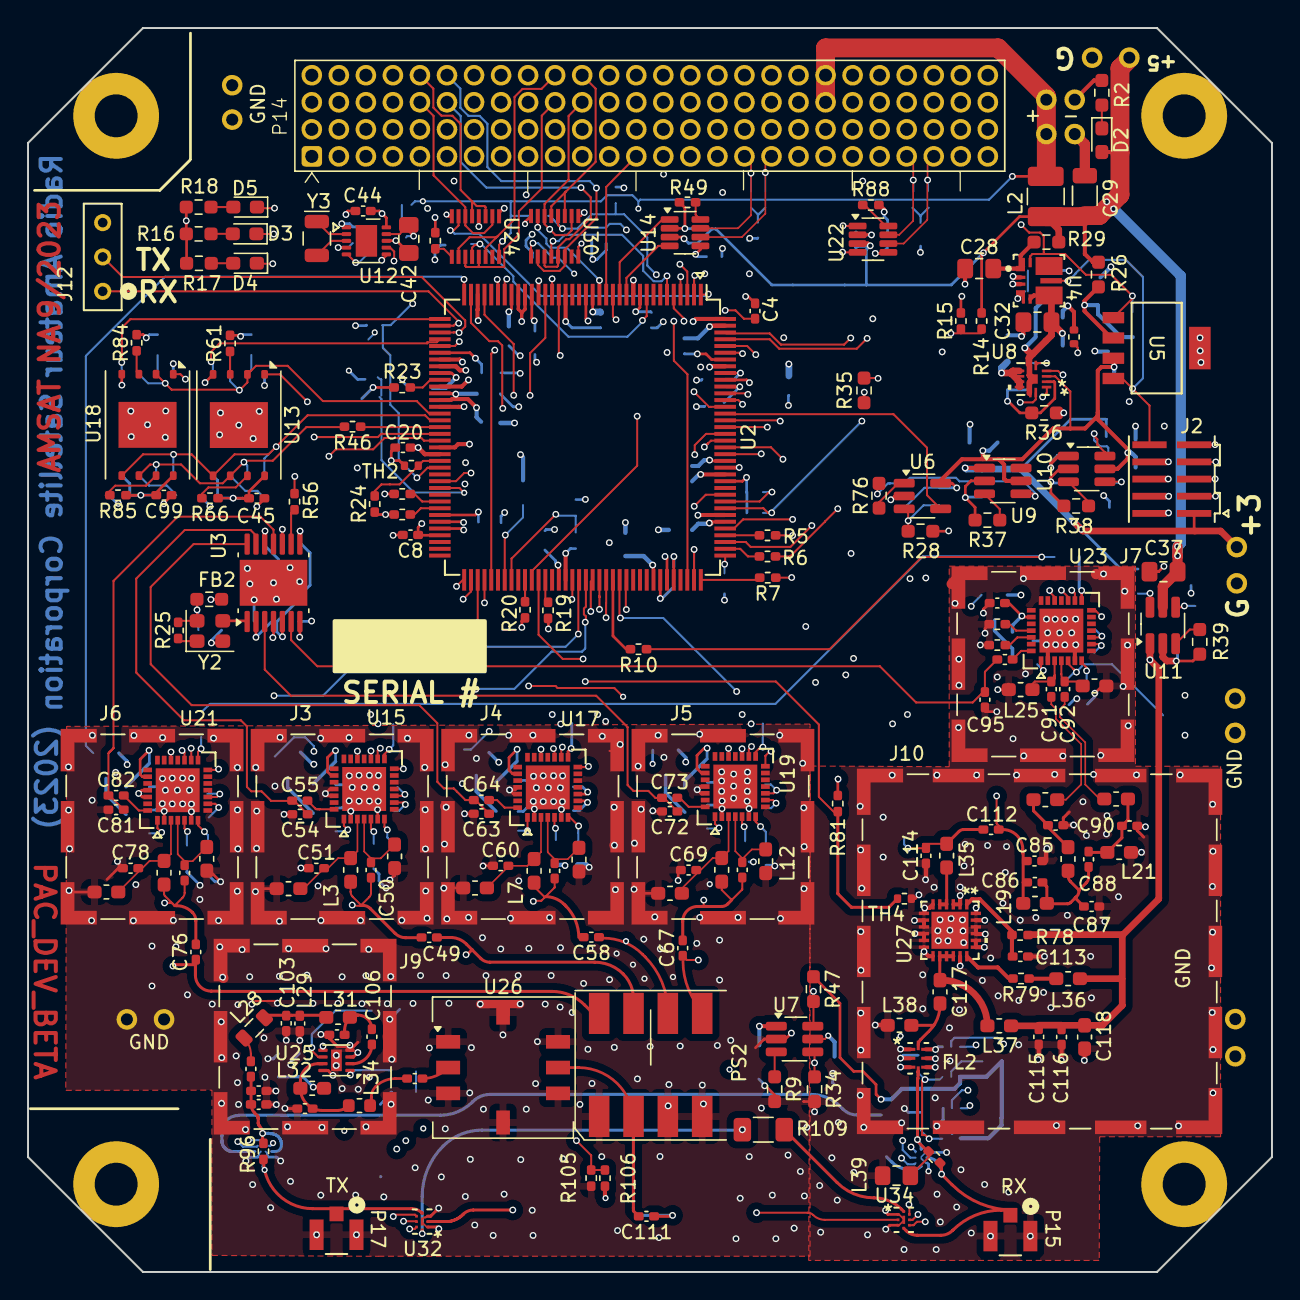
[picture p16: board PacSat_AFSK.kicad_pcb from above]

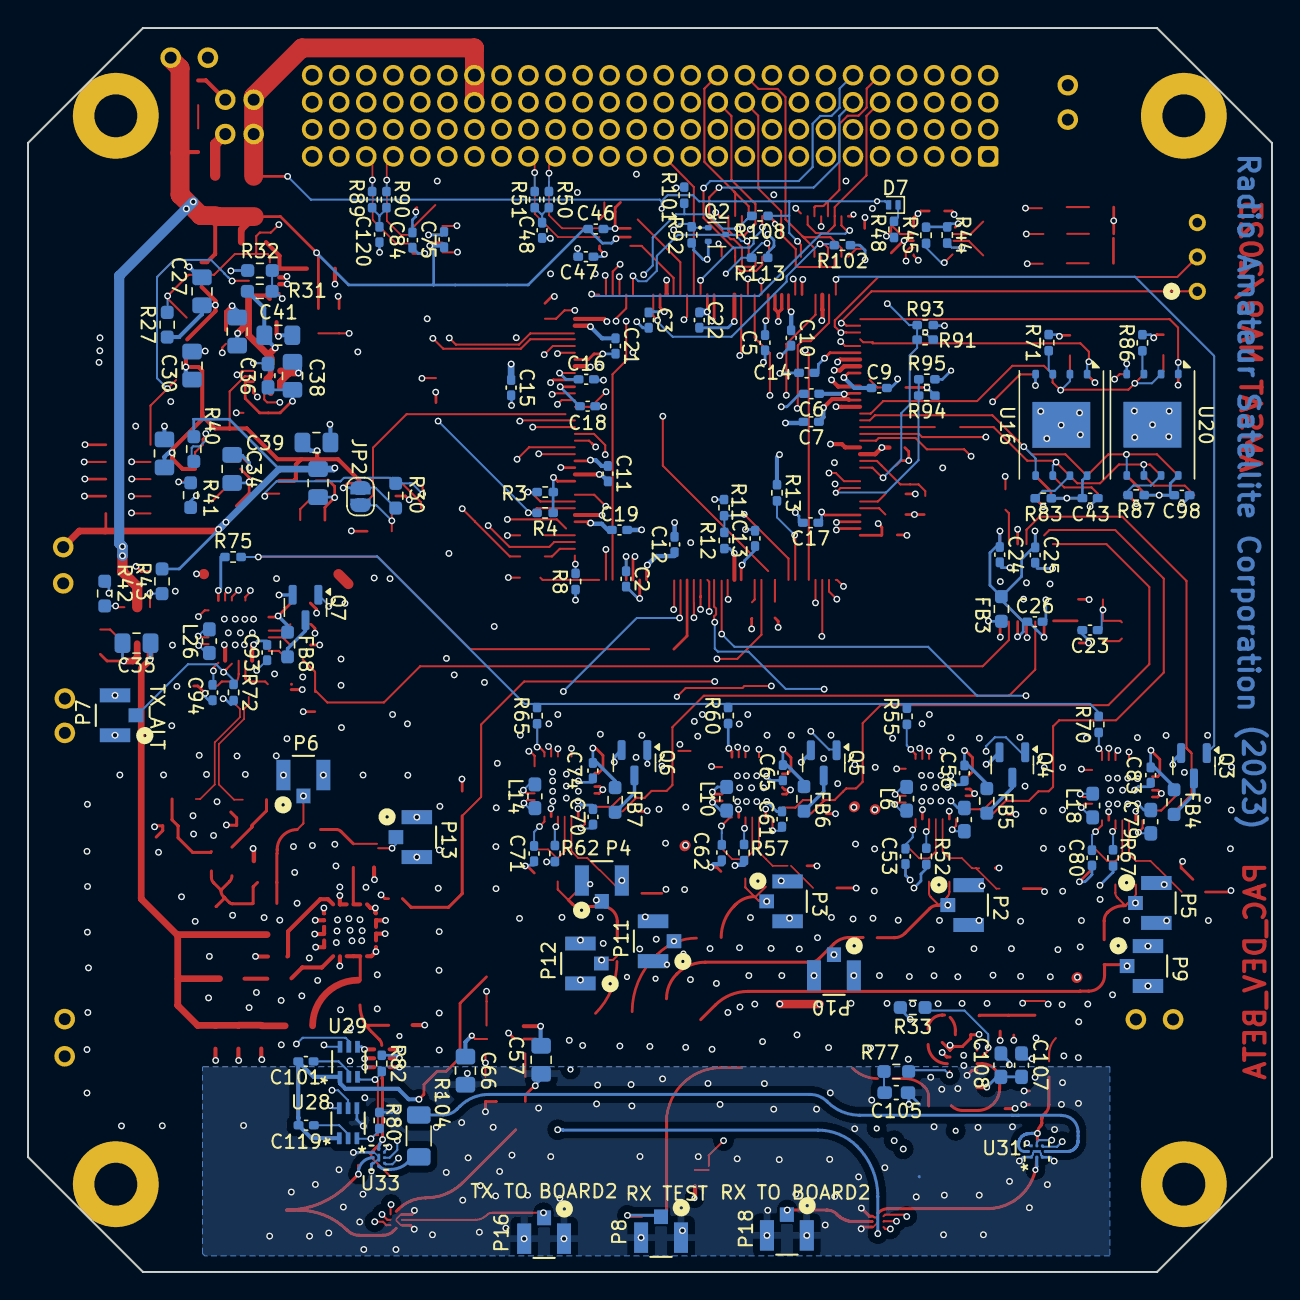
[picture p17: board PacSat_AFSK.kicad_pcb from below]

Board: 6 copper layers, 92.0 x 92.0 mm, 357 parts (150 on the bottom side), 261 nets.

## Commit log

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2025-07-23 Lots of cleanups to fix numerous issues
    [BUS_IO_Interface.kicad_sch, Clocks.kicad_sch, PC104_io_conn.kicad_sch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]
2025-07-24 Add some missing footprints
    I was able to pull them from the PCB.
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2025-07-26 Do a lot of routing work
    RX input is done, 5043s are done, power is done.
    [PacSat_AFSK.kicad_pcb, Power_Amp.kicad_sch, Power_Divider.kicad_sch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]
2025-07-26 Switch regulators to ones with power good
    Tie that into reset.
    [PacSat_AFSK.kicad_pcb, power.kicad_sch, tms570_cpu.kicad_sch]
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2025-07-27 Rework the MRAM and AX5043 SPI connections
    This will greatly simplify routing.
    [PacSat_AFSK.kicad_pcb, tms570_cpu.kicad_sch]
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2025-07-28 Add resistors to the JTAG interface
    They are supposed to be there.
    [BUS_IO_Interface.kicad_sch, PC104_io_conn.kicad_sch, PacSat_AFSK.kicad_pcb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]
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2025-07-28 Added a coplaner connection between the RX filter and hybrid
    Just playing around to see hard hard it is to draw curved traces and set
    up a coplaner.
    [PacSat_AFSK.kicad_pcb]
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2025-07-29 More work on coplanar RX, more RX connector
    The RX connector was too close to the excluded region, move it a bit.
    [PacSat_AFSK.kicad_pcb, Power_Divider.kicad_sch]
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2025-07-29 Add shields around AX5043s, replace UFL connectors
    [PacSat_AFSK.kicad_pcb, Power_Amp.kicad_sch, Power_Divider.kicad_sch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]
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2025-07-30 Move the SPI clock line to the bottom of the board
    That way it's impedance controlled like on the top. Can't use the
    middle that easily unless we add grounding on a signal layer to control
    the impedance.
    Add a ground plane to the non-3.3V portion of the power layer so the
    signal impedance is controlled.
    [PacSat_AFSK.kicad_pcb, Power_Divider.kicad_sch]
2025-07-30 Update SPI clock with simulation
    Simulated the SPI clocks, updated resistor values based on findings.
    [PacSat_AFSK.kicad_pcb, RX_1_ax5043.kicad_sch, RX_2_ax5043.kicad_sch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]
2025-07-30 Rework the AX5043 RX side to a different balun
    It's cheaper (though not smaller) and fits inside the shield.
    [BUS_IO_Interface.kicad_sch, PacSat_AFSK.kicad_pcb, Power_Amp.kicad_sch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]
2025-07-30 Change the AX5043 shield to a frame/cover setup
    Easier access to parts underneath.
    [PacSat_AFSK.kicad_pcb, RX_1_ax5043.kicad_sch, RX_2_ax5043.kicad_sch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]
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2025-07-30 Rework the RF LNA circuitry
    Calculated the input and output impedances and made the proper
    adjustments.
    [PacSat_AFSK.kicad_pcb, Power_Divider.kicad_sch]
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2025-07-31 Replace the 1.2V current limited with a MP5073
    The MAX4495 part that was there wasn't rated for 1.2V.
    [PacSat_AFSK.kicad_pcb, power.kicad_sch]
2025-07-31 Remove the Current Fault for 1.2 and 3.3V
    The didn't go anywhere.
    [PacSat_AFSK.kicad_pcb, power.kicad_sch]
2025-07-31 Add an inverter to drive the 1.2V power limiter enable
    The logic was backwards from the MAX4495 part, so an inverted is needed.
    [PacSat_AFSK.kicad_pcb, power.kicad_sch]
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2025-07-31 Add some missed stuff
    Forgot to hit save...
    [PacSat_AFSK.kicad_pcb]
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2025-07-31 Rework hierarchical sheets
    [BUS_IO_Interface.kicad_sch, PacSat_AFSK.kicad_pcb, PacSat_AFSK.kicad_sch]
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2025-08-01 Rework the LNA impedance matching
    [PacSat_AFSK.kicad_pcb, Power_Divider.kicad_sch]
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2025-08-01 More cleanup around the LNA
    Had the C/L order on the output impedance match wrong.
    Change the double 3pf caps to a 1.5pf, I think a suitable one can be
    found.
    [PacSat_AFSK.kicad_pcb, Power_Divider.kicad_sch]
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2025-08-01 More work on the LNA
    Rework the filter a bit, rework the layout.
    [PacSat_AFSK.kicad_pcb, Power_Divider.kicad_sch]
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2025-08-01 Rework the LNA input filter
    Some more :(
    [PacSat_AFSK.kicad_pcb, Power_Divider.kicad_sch]
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2025-08-02 Fix some markdown issues in the processor pin document
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2025-08-03 Add power measurement on TX
    Add chips for forward and reverse power.
    [PacSat_AFSK.kicad_pcb, Power_Amp.kicad_sch, tms570_cpu.kicad_sch]
2025-08-03 Notes cleanup, add missing footprints
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2025-08-04 Rework AX5043 and PA power enables
    The way they were wasn't going to work, make the enables active high.
    [PacSat_AFSK.kicad_pcb, power.kicad_sch, tms570_cpu.kicad_sch]
2025-08-04 Remove the PA watchdog
    It wasn't doing anything useful.
    Add an enable line from the processor to the TX AX5043.
    [BUS_IO_Interface.kicad_sch, PacSat_AFSK.kicad_pcb, TX_ax5043.kicad_sch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]
2025-08-04 Rework the LNA enable line
    Don't connect +5V through a pullup to a GPIO. That's not in spec
    for the GPIO lines.
    [PacSat_AFSK.kicad_pcb, Power_Divider.kicad_sch, tms570_cpu.kicad_sch]
2025-08-04 Notes cleanups, replace LNA enable MOSFET with BSS138
    [PacSat_AFSK.kicad_pcb, Power_Divider.kicad_sch]
2025-08-04 Replace AX5043 power controls with MOSFETs
    They are simpler, use less power, and are more reliable.
    [PacSat_AFSK.kicad_pcb, RX_1_ax5043.kicad_sch, RX_2_ax5043.kicad_sch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]
2025-08-04 Replace the AX5043 MOSFETs again
    A little wider VTgs and lower on resistance.
    [PacSat_AFSK.kicad_pcb, RX_1_ax5043.kicad_sch, RX_2_ax5043.kicad_sch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]
2025-08-04 Work on the power section
    Move things over to the left a little bit to give more room on the
    right side of the board.
    [PacSat_AFSK.kicad_pcb, power.kicad_sch]
2025-08-04 Change TX bleed off inductor to bigger one
    100nH really isn't big enough.
    [PacSat_AFSK.kicad_pcb, Power_Amp.kicad_sch]
2025-08-04 Move the UFL connectors closer to the traces
    Create less of a stub.
    [PacSat_AFSK.kicad_pcb]
2025-08-04 Remove the ground from KELVIN_GND
    From reading the data sheet, it appears it is not supposed to be
    connected.
    [PacSat_AFSK.kicad_pcb, tms570_cpu.kicad_sch]
2025-08-04 Check over notes and some component values
    Fix a wrong capacitor in one spot, set Q and voltage as necessary.
    [Clocks.kicad_sch, PacSat_AFSK.kicad_pcb, Power_Amp.kicad_sch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]
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2025-08-04 More work on the LNA/PA impedance matchers
    Did some simulations, found some issues.
    [PacSat_AFSK.kicad_pcb, Power_Amp.kicad_sch, Power_Divider.kicad_sch]
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2025-08-05 Fix values of a lot of parts
    Make them standard, 4.1p instead of 4p1, etc.
    Add a tag to a couple of ICs that didn't have a pin 1 indicator on the
    board.
    [BUS_IO_Interface.kicad_sch, Clocks.kicad_sch, PacSat_AFSK.kicad_pcb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]
2025-08-06 Move some pins around and start on the README
    Move pins so that MIBSPI5 is available for use in the future.
    [PacSat_AFSK.kicad_pcb, RX_2_ax5043.kicad_sch, tms570_cpu.kicad_sch]
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2025-08-06 Add some notes, fix the diode footprints on the RTC
    [BUS_IO_Interface.kicad_sch, PacSat_AFSK.kicad_pcb, TX_ax5043.kicad_sch]
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2025-08-07 Change the clock buffer
    Move to one that is temperature rated and has better specs.
    Also reroute one clock line to move it from board edge.
    Get a list of all parts that aren't rated to at least 105C.
    [Clocks.kicad_sch, PacSat_AFSK.kicad_pcb]
2025-08-08 Move the RTC and rework it a bit
    [BUS_IO_Interface.kicad_sch, PacSat_AFSK.kicad_pcb]
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2025-08-08 Forgot to run DRC, fix some issues
    [PacSat_AFSK.kicad_pcb]
2025-08-08 Rework the MRAM device interface
    Use pull ups instead of connecting pins right to +3.3V.
    [BUS_IO_Interface.kicad_sch, PacSat_AFSK.kicad_pcb]
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2025-08-10 More wokr on the PA
    Fix some values on the PA and rearrange a bit to get the inductors
    away from each other.
    [PacSat_AFSK.kicad_pcb, Power_Amp.kicad_sch]
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2025-08-13 Add missing sheets, move active standby to its own hierarchy
    [PacSat_AFSK.kicad_pcb, PacSat_AFSK.kicad_sch, Power_Divider.kicad_sch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]
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2025-08-13 Moved ACTIVE\_N to a normal GPIO so it can be interrupt driven
    [PC104_io_conn.kicad_sch, PacSat_AFSK.kicad_pcb, Power_Divider.kicad_sch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]
2025-08-13 Add OTHER\_HW\_POWER\_N to a GPIO
    So in the externally driven active/standby case the other power state
    can be monitored.
    Also fix issues in the processor pin list.
    [PacSat_AFSK.kicad_pcb, active_standby.kicad_sch, tms570_cpu.kicad_sch]
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2025-08-14 Increase some power track widths
    Make sure they are fat enough to carry the necessary power.
    [PacSat_AFSK.kicad_pcb]
2025-08-14 Move to vertical SMA connectors
    Required quite a bit of rework.
    [rf_in_switch.kicad_sch, rf_out_switch.kicad_sch]
2025-08-14 Change RF connectors to U.FL
    I'll solder a U.FL to SMA connector for testing.
    [rf_in_switch.kicad_sch, rf_out_switch.kicad_sch]
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2025-08-14 Convert a lot of parts to 0402
    The passives across the top where things are crowded.
    [BUS_IO_Interface.kicad_sch, PacSat_AFSK.kicad_pcb, active_standby.kicad_sch]
2025-08-15 Rework passives around the CPU to be 0402
    [BUS_IO_Interface.kicad_sch, PacSat_AFSK.kicad_pcb, tms570_cpu.kicad_sch]
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2025-08-15 Add enable controls for the CAN bus transceivers
    And do some more 0402 conversions.
    [BUS_IO_Interface.kicad_sch, Power_Divider.kicad_sch, power.kicad_sch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]
2025-08-16 Fix impedance matching values, add a simulation
    [Power_Amp.kicad_sch, Power_Divider.kicad_sch]
2025-08-16 Fixed DC bias issue on the output impedance filter of the LNA
    [Power_Amp.kicad_sch, Power_Divider.kicad_sch]
2025-08-16 Replace the output filter with a discrete one
    The part chosen for the output filter didn't have very good ratings with
    respect to being shaken and nothing on thermal cycles. Also, it only
    had 30dB of output filtering. Replace with a discrete filter.
    [Power_Amp.kicad_sch, Power_Divider.kicad_sch, rf_in_switch.kicad_sch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]
2025-08-16 Fix some notes
    [Power_Amp.kicad_sch, rf_in_switch.kicad_sch, rf_out_switch.kicad_sch]
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2025-08-22 Make a little more space around the MRAM
    Change the orientation of some resistors.
    [tms570_cpu.kicad_sch]
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2025-08-24 Lots of updates to ease manufacturing
    Component changes, changes in the formatting of the values, etc.
    [BUS_IO_Interface.kicad_sch, Clocks.kicad_sch, Power_Amp.kicad_sch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]
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2025-08-25 Replace the LNA output filter with discretes
    These take up some more room, but are much cheaper and perform
    quite a bit better.
    [Power_Divider.kicad_sch, TX_ax5043.kicad_sch]
2025-08-25 Update all resistors to have an ohm symbol
    Make it more clean in the BOM what they are.
    [BUS_IO_Interface.kicad_sch, Clocks.kicad_sch, Power_Amp.kicad_sch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]
2025-08-25 Update some inductor values
    Fix some small issues.
    Add a 0 ohm resistor between the LNA output and the filter.
    [Power_Divider.kicad_sch]
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2025-08-25 Change the inductors on the RF input filter
    Use lower resistance ones with higher Q.
    [Power_Divider.kicad_sch]
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2025-08-27 Massive rework of filtering and inductors
    Now that I know how inductors really work.
    [Power_Amp.kicad_sch, Power_Divider.kicad_sch, RX_1_ax5043.kicad_sch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]
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2025-08-27 Rework PA input impedance match
    The two inductor L match works better than the LC match.
    [Power_Amp.kicad_sch]
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2025-08-27 Reset origin to 0,0 to make the board easier to set up
2025-08-27 Do a ton of work to switch to the CubeSat Kit Bus
    Redo the connector, board shape, etc.
    [PC104_io_conn.kicad_sch, power.kicad_sch]
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2025-08-28 Have the BOM file fixer output xls, not csv
    The omega symbol gets translated properly from xls.
    [Clocks.kicad_sch, PC104_io_conn.kicad_sch, RX_1_ax5043.kicad_sch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]
2025-08-28 Finish up temporary PC104 assignments
    Finish up most of what is required for the CubeSat Kit Bus conversion.
    [BUS_IO_Interface.kicad_sch, PC104_io_conn.kicad_sch, tms570_cpu.kicad_sch]
2025-08-28 Add some missing footprints
2025-08-28 Minor fixes for BOM values
    [Clocks.kicad_sch, PC104_io_conn.kicad_sch, Power_Amp.kicad_sch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]
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2025-08-29 Fix POWER_ENABLE to disable 3.3V
    [power.kicad_sch]
2025-08-29 Add an UMBILICAL_ATTACHED signal from the PC104
    Allow the board to know if it is in the launch vehicle. Will
    hardware inhibit transmit.
    [PC104_io_conn.kicad_sch, power.kicad_sch, tms570_cpu.kicad_sch]
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2025-08-30 More prettying up, add some missing footprints
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2025-09-01 A bunch of work on component selections
    And little fixups for things I found.
    [BUS_IO_Interface.kicad_sch, PC104_io_conn.kicad_sch, Power_Amp.kicad_sch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]
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2025-09-01 Add some more UF.L connectors, clean up more stuff
    Allow access to some more points in the RF chain.
    [Power_Amp.kicad_sch, Power_Divider.kicad_sch]
2025-09-01 Renumber shields and PC104 sockets
    Separate out shields into their own designator category.
    Make the PC104 sockets J1 and J2 to make it easier to move to other
    boards.
    [PC104_io_conn.kicad_sch, Power_Amp.kicad_sch, Power_Divider.kicad_sch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]
2025-09-02 Rework the board to be the Fox Plus setup
    [PC104_io_conn.kicad_sch]
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2025-09-02 Replace the 1.2V regulator with a non-module
    It's automotive rated and better for heat cycling.
    [power.kicad_sch, tms570_cpu.kicad_sch]
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2025-09-04 Missed a BOM setting on a part
    [power.kicad_sch]
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2025-09-09 Rename the BOM/POS fixup code
    They can be for any board shop.
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2025-09-09 Add some missing BOM parts
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2025-09-18 Fix some processor pin comments
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
